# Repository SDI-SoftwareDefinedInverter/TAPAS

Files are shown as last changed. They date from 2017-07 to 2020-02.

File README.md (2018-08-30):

## SDI TAPAS - Community Inverter - Quick-Start Guide

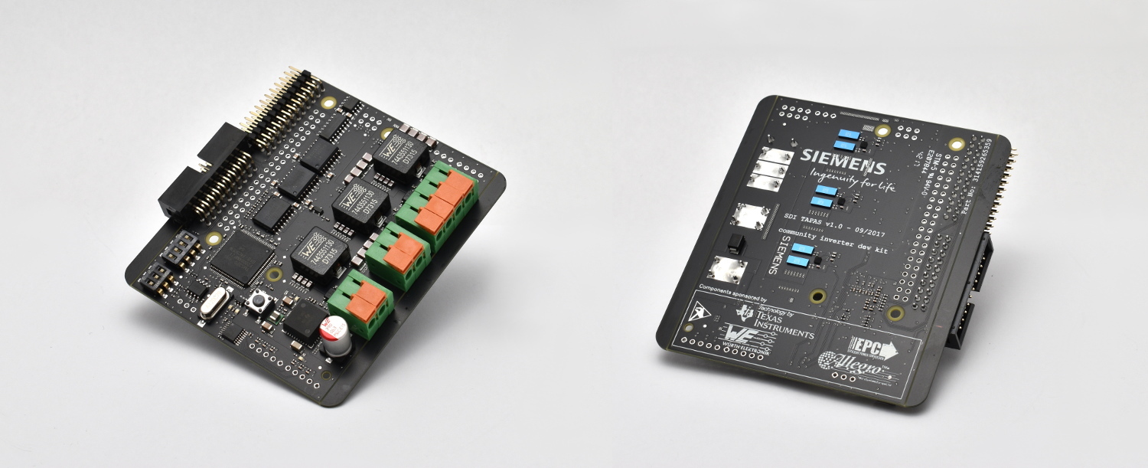
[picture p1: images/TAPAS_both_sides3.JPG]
PCB


Use your TAPAS board with Raspberry PI or Texas Instruments InstaSPIN

__!CAUTION!__

__The TAPAS community inverter board is not a toy!__ It is __intended for
laboratory use only and may only be operated by experienced personell (engineers, scientists, qualified makers). Never use it in a productive or potentially explosive environment! Never operate without supervision!__
(see section 6)

The TAPAS board as well as connected devices can get __very hot, never touch during	
operation and/or cool-down period. Always use an appropriate case.__ 

__If the TAPAS board is used in conjunction with mechanical,
electromagnetic, acoustic, optical or other components,__ e.g. a motor
drive, __significant forces can occur. Always ensure safety, containment and (mechanical) stability of the
entire set-up including case, base-plate and/or table! Prevent direct physical contact, always place set-up
in an appropriate case, employ safe software techniques__ (e.g. torque and temperature
limiting) and __limit the supply current and voltage (strictly <=48V).__

__Only enable power supply if set-up is secured in case.__

<table style="width:100%;background-color:white" cellspacing="0" cellpadding="0" border="0" >
  <tr>
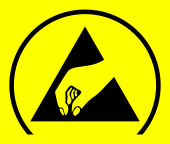
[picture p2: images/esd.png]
    <th><br>
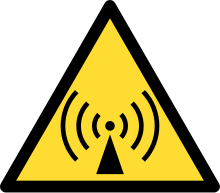
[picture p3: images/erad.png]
	 </th>
	  <th align="left"><b>
	  The TAPAS board is very sensitive to electrostatic discharge - handle with	
		  care! Never touch the board if the supply voltage is turned on!<br>
		  <br>		
The TAPAS board may emmit electromagnetic radiation! Do not operate the board in proximity to devices that are susceptible to electromagnetic interference. Do not operate if pacemaker patients are in the room.
		  </b>
	  </th>	  
  </tr>
</table>

## Foreword and acknowledgements

This board (TAPAS) is intended to train the next generation of power 
electronics researchers and (application) engineers.
It is designed as an educational platform that addresses enthusiasts as well as experts at
universities and in the industry. 

TAPAS features a 48V, 3-phase GaN power stage with on-board filters. This
design-choice allows for a high switching frequency/bandwidth (300kHz 
and beyond) whilst producing a smooth output wave-form. In contrast, 
commonly available IGBT or MOSFET converter boards typically have a 
rather limited bandwidth and/or produce a square output wave-form.

This unique feature of high bandwidth and smooth output makes TAPAS to 
some degree universal, giving rise to educational applications in AC and DC 
[drives](https://www.youtube.com/watch?v=yvK9VINiwhw&feature=youtu.be), DC/DC power conversion, [audio](https://www.youtube.com/watch?v=IIk90JD8xEQ), robotics, magnetic field control, 
battery charging, etc. Note that universality is achieved with a single, fixed 
hardware platform where the overall functionality is defined via software 
(changes) only – the reason why we coined the term “Software Defined 
Inverter” (SDI). 

TAPAS is designed of Raspberry PI and multiple boards can be used in 
collaboration, giving rise to many-phase applications such as quadrocopters 
or multi-axis servo control. Together with open-source code examples and 
extensive documentation we made TAPAS as accessible to the community as 
possible.

To help us make TAPAS affordable, we would like to thank our friends 
and partners at Texas Instruments, Efficient Power Conversion (EPC), Würth 
Elektronik and Allegro Micro who sponsored most of the active and passive 
components on the board (see bill of materials). I hope you will have as much 
fun with TAPAS as we had making it.

Dominic Buchstaller - concept, lead-design - TAPAS

*For a more visual motivation also see the [TAPAS slide deck](https://github.com/SDI-SoftwareDefinedInverter/TAPAS/blob/master/SDI_TAPAS_introduction.pdf).*

__Created by :__

SIEMENS LOGO

_SIEMENS SDI (Software Defined Inverter)_ \* in-house start-up for I/Os

__Components sponsored by:__

SPONSORS LOGO

_Texas Instruments_ <http://www.ti.com>

_Efficient power conversion (EPC)_ <http://epc-co.com>

_WÜRTH ELEKTRONIK_ <http://www.we-online.com>

_Allegro Microsystems_ <http://www.allegromicro.com>

## 1. INTRODUCTION	

This quick-start-guide will lead you through the necessary steps to get TAPAS
up and running with most commercially available DC-brushless motors.
If you are new to Texas Instruments DSPs or power conversion, we advise you	
to start with this guide. It will take you through the necessary steps to set-up 
your (coding) environment and bring the board to life. You are then free to
explore the endless possibilities that the platform provides.

### TAPAS key characteristics
+ DC-Input 12V - 48V
+ Maximum DC / AC (per phase) current - 30A
+ Up to 300W continuous power - passively cooled (@>120kHz switching frequency)
+ Switching frequency up to 600 kHz at reduced load
+ On-board output-filter enables smooth output voltage
+ Texas Instruments C2000 Piccolo (TMS320F28069M) DSP - InstaSPIN MOTION-enabled
+ CAN, GPIO, UART, SPI, 2 x QEP (encoder) interface onboard
+ Raspberry-Pi compatible

### Notice
+ Never exceed 48V operating voltage and ensure correct polarity of the power supply. Incorrect polarity will destroy the board.
+ Never short-circuit the inverter output and never enable high- and low-side switches at the same time. Always ensure the minimum dead time between switching high- and low-side switches of half-bridges. Failure to do so will most likely destroy the board.
+ In case of board failure, disconnect power source immediately. Never inhale fumes comming from the board.
+ Never disconnect the power source from the board while in operation, this may damage or destroy the board.
+ Only connect appropriate loads/sources to the board, inappropriate loads/sources (e.g. high powered generators) may damage the board
+ In order to use TAPAS with motor drives some basic information is required, in particular number of pole pairs and maximum rated current.

### TAPAS pinout
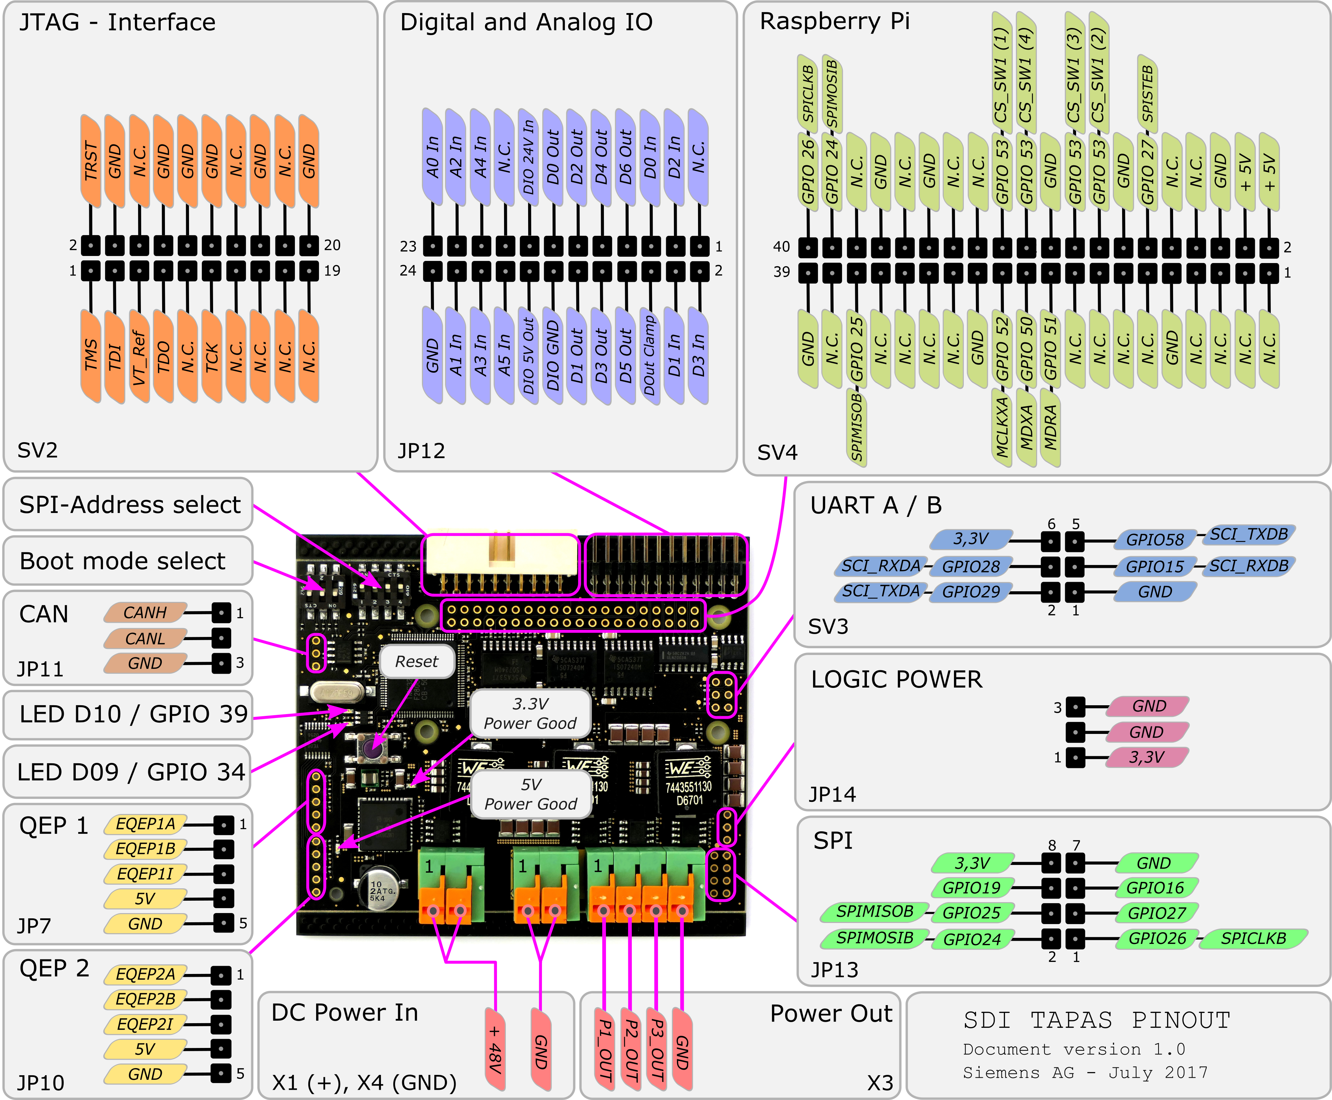
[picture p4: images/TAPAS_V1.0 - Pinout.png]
TAPAS PINOUT Figure1 : TAPAS pinout


### Box contents
+ TAPAS board
+ This quick-start guide
+ An SDI sticker
+ 7 (optional) board-connectors (JP7, JP10, JP11, JP13, JP14, SV3, SV4) for hand-soldering

### Required materials 
To get started with TAPAS you will need the following (additional) items.

+ We highly recommend placing TAPAS in __a case__. This will keep your TAPAS board safe.
The 3D model for our very own case can be found and downloaded here:
<https://github.com/SDI-SoftwareDefinedInverter/TAPAS/blob/master/TAPAShousing.zip>. 
If you don't own a 3D printer, many local 3D printing services are available on-line.
Print with temperature-stable materials like ABS (not PLA).				
+ __DC power supply__ with a minimum of 12V and >3A continuous current output.
Alternatively, you may use any battery with the correct voltage and an appropriate
fuse in the supply line	
+ A __DC brushless motor__	
+ If you want to start programming with TAPAS you will need a __JTAG programmer__.
We recommend using the OLIMEX TMS320-JTAG-USB XDS100-V2. Alternatively, you can use the newer version of this 
USB-JTAG-emulator called TMS320-XDS100v3+, there you have to leave all the jumpers open and use the __TI_JTAG_20__ 
connector to connect to your TAPAS-board with a 20pin 1:1 wired cable. 
+ If you want to use TAPAS with __Raspberry PI__ we recommend a Raspberry PI Zero (W)
+ If you want to use TAPAS with __Raspberry PI__ we also recommend the following parts for mechanical stability: 
	+ 4 screws M2,5 x 6mm (plastic)	
	+ 4 screw nuts M2,5 (plastic)
	+ 4 spacers M2,5 x 10mm with one male and one female thread (plastic)
	+ 12 washers M2,5 (plastic)

### Note: Difference between FIKAT (TAPAS pre-release version) and TAPAS (release version)
There are some PCB differences between the pre-release version (code-name FIKAT - PCB with Siemens & SDI logo) and release version 1.0 (code-name TAPAS - PCB with Siemens and manufacturer logos)

+ The connector of the OLIMEX JTAG programmer does not pysically fit into the JTAG-interface connector SV2 on FIKAT (it is too wide). You will have to solder a simple 1:1 adapter to make it work (see ugly example below). This has been fixed in TAPAS.  
+ TAPAS has more PINs of the Raspberry-Pi socket (SV4) connected to GND. On FIKAT only pins 34 and 39 are connected to GND. Hence 
you cannot use a Nano Pi with FIKAT as the GND connection is missing.
+ The SPI-Chip select signal (GPIO53) is connected to pin26 of SV4 via the address DIP-switch (2) on FIKAT. This has moved to pin 
16 of SV4 on TAPAS.
+ The resistors R\_TXA1, R\_RXA1, R\_TXB1 and R\_RXB1 are populated on FIKAT but not on TAPAS.
+ The 0Ohm gate resistors R19, R23, R20, R24, R12, R14, R16, R15, R17, R18, R22, R21 on FIKAT have been changed to 2,2Ohm on 
TAPAS
+ The DC-bus capacitor C10 for the 5V-voltage regulator U99 has been upgraded from a standard SMD-electrolytic type on FIKAT to a 
39µF polymer type on TAPAS. It can now handle a higher DC ripple current on the dc-bus
+ We added a TVS-clamping-diode for DC over voltage protection on TAPAS. (Not available on FIKAT). This is to absorb some of the 
breaking energy if the user forgot to use a breaking chopper
+ The isolation ICs IC5, IC6 and IC7 on FIKAT have been swapped for a different type on TAPAS  - this should have no influence on 
the behaviour
+ The current sensors on FIKAT are 20A bidirectional types, this has been changed to a 30A bidirectional type on TAPAS

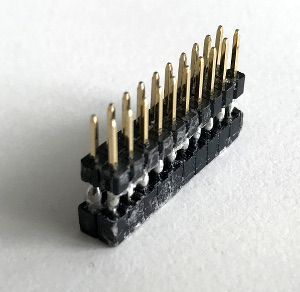
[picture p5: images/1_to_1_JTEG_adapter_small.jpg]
JTAG ADAPTER Figure1 : JTAG ADAPTER


## 2. GETTING STARTED WITH TAPAS AND RASPBERRY PI 
### (FOR LABORATORY USE ONLY)
###
### Note: TI Instaspin motor identification is not 100% reliable for every motor. Success depends on motor type, supply voltage and supply current (see below).
### Note: The stock firmware limits the board current to 6A and the board temperature to 80°C

+ Create an SD-Card image for your Raspberry Pi Zero (W)
(<https://www.raspberrypi.org/documentation/installation/installing-images/>)
+ Insert SD card in Raspberry PI Zero (W) and check that the Raspberry PI boots to a command prompt
+ Make sure that you have a working Python 3.0 and git installation

```
python --version
git --version
```
+ Get the TAPAS software and documentation package from 
<https://github.com/SDI-SoftwareDefinedInverter/TAPAS>
and place it into your home folder

```
cd
git clone https://github.com/SDI-SoftwareDefinedInverter/TAPAS.git
```
+ If successful, halt your Raspberry PI

```
sudo halt
```
+ Set the SPI-Address select DIP switch to (ON)-(OFF)-(OFF)-(OFF) for the switch 
positions from (1) - (4) (see pinout)
+ Disconnect the Raspberry PI from any power source and plug it into the TAPAS
Raspberry PI board connector (see pinout).
+ Connect your TAPAS board to a DC power supply and to a DC brushless motor (see pinout).
+ Set the supply voltage to 24V with 5A current limit and turn it on
+ If your motor does not start turning, increasing the supply voltage may help (
+ Log into your Raspberry PI and type

```
cd ~/TAPAS
python3 TAPASstart.py
```
+ Then follow the prompts on the monitor
+ If the identification fails, repeat the process and increase current/voltage limit
+ HINT: It is strongly recommended to never run the application without any motor or load connected to the terminals!

## 3. GETTING STARTED WITH TAPAS AND SIEMENS IoT2000
### (FOR LABORATORY USE ONLY)

It is rather straightforward to use TAPAS with SIMATIC IOT2000. This will allow you to build Siemens MindSphere connected drives applications and more. All you need is a few jumper-cables to connect their respective SPI interfaces.

SIMATIC IOT2040 connected to TAPAS

Required steps on SIMATIC IOT2000:
+ set-up SIMATIC IOT2000 with image V2.1.4
+ set the IO-level jumper to 3.3V (right-most jumper to right position)
+ enable SIMATIC IOT2000 SPI-interface:
```
iot2000setup
```
+ add the spidev  python library:
```
pip3 install spidev
```
+ connect the jumper cables as follows:
 
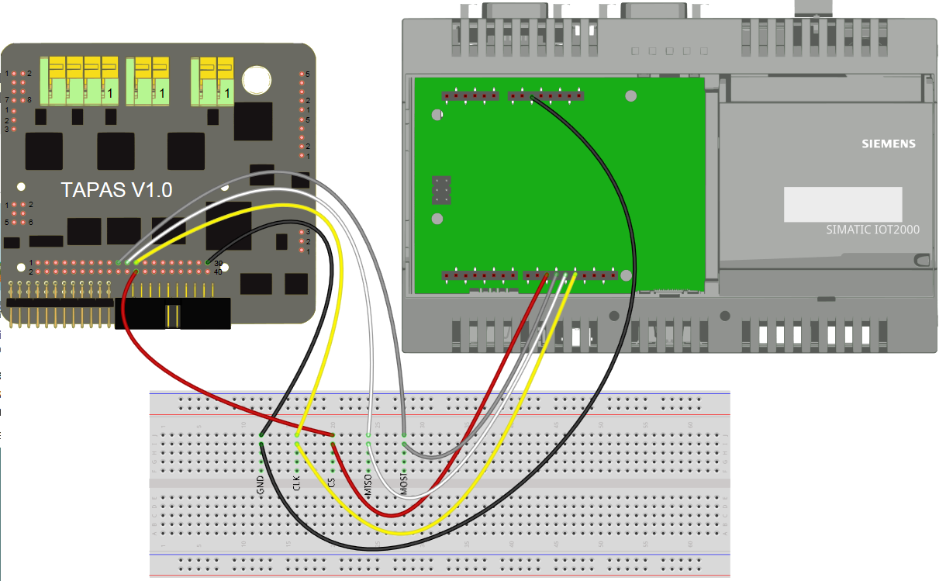
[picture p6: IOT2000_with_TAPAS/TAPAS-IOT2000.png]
SIMATIC IOT2040 - TAPAS connection instructions


+ ensure that the DIP-switch SW1 is set to ON-OFF-OFF-OFF (from position 1 to 4)
+ as git is not available on the IOT2000 platform you have to download the TAPAS-repository from github and transfer it to the IOT2000 by hand (e.g. via scp, putty, USB-Stick ... ). Then unpack it. 
+ run the TAPASstart python script: 
```
python3 TAPASstart.py
```
HINTS: 

You can find a simplified fritzing part for TAPAS here: 

<https://github.com/SDI-SoftwareDefinedInverter/TAPAS/tree/master/Fritzing_part_TAPAS>

You can find a simplified fritzing part for the SIMATIC IOT2040 and the fritzing project used to generate the cabling diagram here: 

<https://github.com/SDI-SoftwareDefinedInverter/TAPAS/tree/master/IOT2000_with_TAPAS/Fritzing>
 
Additonal images are located here: 
 
<https://github.com/SDI-SoftwareDefinedInverter/TAPAS/tree/master/IOT2000_with_TAPAS>

## 4. GETTING STARTED WITH TAPAS AND CODE COMPOSER STUDIO
### (FOR LABORATORY USE ONLY)
__!CAUTION!__	

__The stock TAPAS firmware implements software features that ensure safe operation.
Changing the stock TAPAS firmware may damage or destroy your TAPAS board, lead to
harm and/or danger. Make sure that you fully understand the supplied sample code and
the underlying principles before flashing your own firmware.__

For programming the TAPAS-Board, we recommend Code Composer Studio from Texas Instruments.
It is free of charge and can be downloaded from here:

<http://processors.wiki.ti.com/index.php/Download_CCS>

Choose the correct setup-package for your OS and install it following the instructions in
the installation-wizard.

The drivers for the OLIMEX JTAG-Debug probe are included in the standard installation
package. If you choose a JTAG Programmer from another vendor make sure that you installed
the correct drivers and that it is compatible with code composer studio.

To be able to use the InstaSpin capabilities of the DSP, you require motorware version
1\_01\_00\_16. Install git for your operating system and clone the repository in the same
way, you did it for the Raspberry Pi:

```
git clone https://github.com/SDI-SoftwareDefinedInverter/TAPAS.git
```

We included a copy of TI motorware in the cloned repository (_`motorware.zip`_). Alternatively you can download motorware from Motorware or here <https://github.com/SDI-SoftwareDefinedInverter/TAPAS/blob/master/motorware.zip>.

As the TAPAS board definition is not part of the stock motorware package we have to make some modifications to it. All the necessary changes are contained in the patch-file _`SDITAPASmotorwarePatch.patch`_. Now copy _`SDITAPASmotorwarePatch.patch`_ to the motorware installation folder (usually _`C:\ti\`_) and start git in bash mode (also in the motorware installation folder). Then execute the following commands:

```
dos2unix SDITAPASmotorwarePatch.patch
patch -p0 -i SDITAPASmotorwarePatch.patch
```

This completes the installation of motorware and you can start playing with the motorware-labs
and the quick-start demo firmware. To add the quick-start project, start Code Composer 
Studio and choose a workspace location. Close the welcome-window and then select 
"Project-\>Import CCS Projects..." In the upcoming window choose the option "Select search-directory"
and click the "Browse" - button. Navigate to the directory of your motorware installation,
go to the folder
_`<drive>:\ti\motorware\motorware_1_01_00_16\sw\solutions\instaspin_foc\boards\TAPAS_V1_0\f28x\f2806xF\projects\ccs5\`_
and click the "OK" button.

In the "Discovered projects" - list below you will see all the projects in the selected directory.
Here you can choose, for example, the _"TAPAS\_quick\_start"_ project which represents the stock demo firmware to be used with the python - script for Raspberry PI.

For all the other projects in the folders _`<drive>:\ti\motorware\motorware_1_01_00_16\sw\solutions\instaspin_foc\boards\TAPAS_V1_0\f28x\f2806xF\projects\ccs5\`_
and _`<drive>:\ti\motorware\motorware_1_01_00_16\sw\solutions\instaspin_motion\boards\TAPAS_V1_0\f28x\f2806xF\projects\ccs5\`_ please consider the _"InstaSPIN Projects and Labs User's 
Guide"_ which comes with the motorware-installation and is located 
in _`<drive>:\ti\motorware\motorware_1_01_00_16\docs\labs\instaspin_labs.pdf`_ of the motorware 
installation.There you can find further 
information on how to compile the firmware, start a debugging session, 
flash the DSP and get an impression, what all the program components 
actually do. Please keep in mind that all the labs that are designed 
to drive two motors independently are skipped - this is not possible 
with TAPAS because there is only one 3-phase power stage.

To be able to run our TAPAS demo-webapp you also require the InstaSPIN-UNIVERSALGUI from Texas Instruments which you can get here:

<http://www.ti.com/tool/INSTASPINUNIVERSALGUI>

You have now completed the installation of the TAPAS development environment. 
We have also created a TAPAS-webapp to test all external I/O hardware. 
You can download it from:	

```
https://github.com/SDI-SoftwareDefinedInverter/TAPAS/blob/master/
TAPASwebapp.zip
```
Unzip the file place it in:

```
<drive>:\ti\guicomposer\webapps\
```

## 5. FREQUENTLY ASKED QUESTIONS / TROUBLE SHOOTING

Q: Where can I get a TAPAS board?

A: The TAPAS board is provided for free – just write a few lines to tapas.support.ct@siemens.com what you intend to do with it. For legal reasons we are limited to ship the board only within the EU atm - we are working on expanding this limitation.

Q: Where can I find example projects?

A: You can find use cases and a number of user build projects on the community site <https://challenge.tapas.sdi.tools/>

Q: Can I use other JTAG-Programmers than the OLIMEX?

A: Yes you can. As long as it's 3,3V compatible and supported by Code Composer Studio it should work.

Q: Can I run the board at full power for longer periods of time?

A: Yes you can. In that case it is important to manage the board temperature. We recommend adding some temperature monitoring code (see examples)
and dynamically limit the output current. Keep the board temperature below 90°C at all times to keep your TAPAS board healthy.

Q: If I abruptly reduce the speed of my motor why is the JTAG-connection interrupted or other funny things happen?

A: It is very likely that you are using a DC power supply and not a battery to power TAPAS. The breaking energy is fed back into the DC supply and
causes an abrupt rise in DC voltage. Note that although TAPAS is designed to absorb some breaking energy, excessive DC voltage peaks may damage the
board. To prevent this effect, limit the rate of change in motor velocity, use a battery instead of a DC power supply or invest in a current sink
(breaking chopper).

Q: My motor is making some noise but does not start turning during the identification procedure from the examples. 

A: Slightly increase the supply voltage for the TAPAS-board and retry the identification of your motor. Never exceed
48V supply voltage as this will damage or even destroy your board! Also check the current rating of your motor again
and make sure you have set it correctly.

Q: I get an overcurrent protection message during motor identification in your Raspberry PI example. 

A: If this happens once, just retry the identification procedure. If this happens permanently, check your current rating again. 
Always keep in mind that the curent sensors on TAPAS can only measure +-30A at their maximum.

## 6. REFERENCES

The following documents can be helpful in developing with TAPAS:

+ TAPAS Pinout: 
<https://github.com/SDI-SoftwareDefinedInverter/TAPAS/blob/master/TAPAS-Pinout.pdf>	
+ TAPAS Schematics: 
<https://github.com/SDI-SoftwareDefinedInverter/TAPAS/blob/master/TAPAS-Schematic.pdf>
+ This 13document(quick start guide):
<https://github.com/SDI-SoftwareDefinedInverter/TAPAS/blob/master/TAPAS_quickStartGuide.pdf>
+ InstaSPIN-FOC and InstaSPIN-MOTION user guide : 
<http://www.ti.com/lit/ug/spruhj1g/spruhj1g.pdf>
+ Instaspin projects and labs user's guide, see motorware _`<drive>:\ti
\motorware\motorware_1_01_00_16\docs\labs\instaspin_labs.pdf`_
+ TMS320F28069MPZT overview and datasheet: 
<http://www.ti.com/lit/ug/spruh18g/spruh18g.pdf>

## 7. STANDARD TERMS FOR EVALUATION MODULES

1 Delivery: Siemens delivers TAPAS community converter boards (collectively, a “TAPAS BOARD or “TAPAS BOARDS”) to the User (“User”) free of charge in accordance with the terms set forth herein. User's acceptance of the TAPAS BOARD is expressly subject to the following terms.

1.1 TAPAS BOARDS ARE INTENDED SOLELY FOR PRODUCT OR SOFTWARE DEVELOPERS FOR USE IN A RESEARCH AND DEVELOPMENT SETTING TO FACILITATE FEASIBILITY EVALUATION, EXPERIMENTATION OR SCIENTIFIC ANALYSIS.  TAPAS BOARDS HAVE NO DIRECT FUNCTION AND ARE NOT FINISHED PRODUCTS. TAPAS BOARDS SHALL NOT BE DIRECTLY OR INDIRECTLY ASSEMBLED AS A PART OR SUBASSEMBLY IN ANY FINISHED PRODUCT. 

1.2 TAPAS BOARDS ARE NOT INTENDED FOR CONSUMER OR HOUSEHOLD USE. TAPAS BOARDS MAY NOT BE SOLD, SUBLICENSED, LEASED, RENTED, LOANED, ASSIGNED, OR OTHERWISE DISTRIBUTED FOR COMMERCIAL PURPOSES BY USERS, IN WHOLE OR IN PART, OR USED IN ANY FINISHED PRODUCT OR PRODUCTION SYSTEM.

2 Return and replacement:
Due to the fact that Siemens delivers the TAPAS BOARDS free of charge and for use in research and development settings only, Siemens will not provide any warranty with regard to any specifications of the TAPAS BOARDS. If the User notifies Siemens of any defects within thirty (30) days after delivery, Siemens will replace the respective TAPAS BOARD, provided that User returns the TAPAS BOARD within the 30-day-period to Siemens. Siemens will not provide any warranty for any replaced TAPAS BOARDS. 

3 Regulatory Notices:

3.1 European Union

3.1.1 For TAPAS BOARDs subject to EU Directive 2014/30/EU (Electromagnetic Compatibility Directive): This is a class A product intended for use in environments other than domestic environments that are connected to a low-voltage power-supply network that supplies buildings used for domestic purposes. In a domestic environment this product may cause radio interference in which case the user may be required to take adequate measures. 

4 TAPAS BOARD Use Restrictions and Warnings:

4.1 TAPAS BOARDS ARE NOT FOR USE IN FUNCTIONAL SAFETY AND/OR SAFETY CRITICAL EVALUATIONS, INCLUDING BUT NOT LIMITED TO EVALUATIONS OF LIFE SUPPORT APPLICATIONS.

4.2 User must read and follow the Quickstart Guide  provided by Siemens regarding the TAPAS BOARD prior to handling or using the TAPAS BOARD, including without limitation any warning or restriction notices. The notices contain important safety information related to, for example, temperatures and voltages.

4.3 Safety-Related Warnings and Restrictions:

4.3.1 User shall operate the TAPAS BOARD within Siemens’s recommended specifications and environmental considerations stated in the user guide, other available documentation provided by Siemens, and any other applicable requirements and employ reasonable and customary safeguards. Exceeding the specified performance ratings and specifications (including but not limited to input and output voltage, current, power, and environmental ranges) for the TAPAS BOARD may cause personal injury or death, or property damage. If there are questions concerning performance ratings and specifications, User should contact a Siemens TAPAS representative via the github issue tracker (https://github.com/SDI-SoftwareDefinedInverter/TAPAS/issues) prior to connecting interface electronics including input power and intended loads. Any loads applied outside of the specified output range may also result in unintended and/or inaccurate operation and/or possible permanent damage to the TAPAS BOARD and/or interface electronics. Please consult the TAPAS BOARD quick start guide prior to connecting any load to the TAPAS BOARD output. If there is uncertainty as to the load specification, please contact a Siemens field representative. During normal operation, even with the inputs and outputs kept within the specified allowable ranges, some circuit components may have elevated case temperatures. These components include but are not limited to linear regulators, switching transistors, pass transistors, current sense resistors, and heat sinks, which can be identified using the information in the associated documentation. When working with the TAPAS BOARD, please be aware that the TAPAS BOARD may become hot.

4.3.2 TAPAS BOARDs are intended solely for use by technically qualified, professional electronics experts who are familiar with the dangers and application risks associated with handling electrical mechanical components, systems, and subsystems. User assumes all responsibility and liability for proper and safe handling and use of the TAPAS BOARD by User or its employees, affiliates, contractors or designees. User assumes all responsibility and liability to ensure that any interfaces (electronic and/or mechanical) between the TAPAS BOARD and any human body are designed with suitable isolation and means to safely limit accessible leakage currents to minimize the risk of electrical shock hazard. User assumes all responsibility and liability for any improper or unsafe handling or use of the TAPAS BOARD by User or its employees, affiliates, contractors or designees.

4.4 User assumes all responsibility and liability to determine whether the TAPAS BOARD is subject to any applicable international, federal, state, or local laws and regulations related to User’s handling and use of the TAPAS BOARD and, if applicable, User assumes all responsibility and liability for compliance in all respects with such laws and regulations. User assumes all responsibility and liability for proper disposal and recycling of the TAPAS BOARD consistent with all applicable international, federal, state, and local requirements.

5 Accuracy of Information: To the extent Siemens provides information on the availability and function of TAPAS BOARDS, Siemens attempts to be as accurate as possible. However, Siemens does not warrant the accuracy of TAPAS BOARD descriptions, TAPAS BOARD availability or other information on its websites as accurate, complete, reliable, current, or error-free.

6 Disclaimers:

6.1 EXCEPT AS SET FORTH IN SECTION 2, SIEMENS DISCLAIMS ALL OTHER WARRANTIES, EXPRESS OR IMPLIED, REGARDING THE TAPAS BOARDS, INCLUDING BUT NOT LIMITED TO ANY WARRANTY OR IMPLIED WARRANTIES OF MERCHANTABILITY OR FITNESS FOR A PARTICULAR PURPOSE OR NON-INFRINGEMENT OF ANY THIRD PARTY PATENTS, COPYRIGHTS, TRADE SECRETS OR OTHER INTELLECTUAL PROPERTY RIGHTS.

6.2 EXCEPT FOR THE LIMITED RIGHT TO USE THE TAPAS BOARD SET FORTH HEREIN, NOTHING IN THESE TERMS SHALL BE CONSTRUED AS GRANTING OR CONFERRING ANY RIGHTS BY LICENSE, PATENT, OR ANY OTHER INDUSTRIAL OR INTELLECTUAL PROPERTY RIGHT OF SIEMENS, ITS SUPPLIERS/LICENSORS OR ANY OTHER THIRD PARTY, TO USE THE TAPAS BOARD IN ANY FINISHED END-USER OR READY-TO-USE FINAL PRODUCT, OR FOR ANY INVENTION, DISCOVERY OR IMPROVEMENT, REGARDLESS OF WHEN MADE, CONCEIVED OR ACQUIRED.

7 User's indemnity obligations and representations: USER WILL DEFEND, INDEMNIFY AND HOLD SIEMENS, ITS LICENSORS AND THEIR REPRESENTATIVES HARMLESS FROM AND AGAINST ANY AND ALL CLAIMS, DAMAGES, LOSSES, EXPENSES, COSTS AND LIABILITIES (COLLECTIVELY, "CLAIMS") ARISING OUT OF OR IN CONNECTION WITH ANY HANDLING OR USE OF THE TAPAS BOARD THAT IS NOT IN ACCORDANCE WITH THESE TERMS. THIS OBLIGATION SHALL APPLY WHETHER CLAIMS ARISE UNDER STATUTE, REGULATION, OR THE LAW OF TORT, CONTRACT OR ANY OTHER LEGAL THEORY, AND EVEN IF THE TAPAS BOARD FAILS TO PERFORM AS DESCRIBED OR EXPECTED.

8 Limitations on Damages and Liability:

8.1 General Limitations. IN NO EVENT SHALL SIEMENS BE LIABLE FOR ANY SPECIAL, , INDIRECT, , INCIDENTAL OR CONSEQUENTIAL, DAMAGES IN CONNECTION WITH OR ARISING OUT OF THESE TERMS OR THE USE OF THE TAPAS BOARDS. EXCLUDED DAMAGES INCLUDE, BUT ARE NOT LIMITED TO, COST OF REMOVAL OR REINSTALLATION, ANCILLARY COSTS TO THE PROCUREMENT OF SUBSTITUTE GOODS, RETESTING, OUTSIDE COMPUTER TIME, LABOR COSTS, LOSS OF GOODWILL, LOSS OF PROFITS, LOSS OF SAVINGS, LOSS OF USE, LOSS OF DATA, OR BUSINESS INTERRUPTION. NO CLAIM, SUIT OR ACTION SHALL BE BROUGHT AGAINST SIEMENS MORE THAN TWELVE (12) MONTHS AFTER THE EVENT THAT GAVE RISE TO THE CAUSE OF ACTION HAS OCCURRED.

8.2 Specific Limitations. IN NO EVENT SHALL SIEMENS’ AGGREGATE LIABILITY FROM ANY USE OF A TAPAS BOARD PROVIDED HEREUNDER, INCLUDING FROM ANY WARRANTY, INDEMITY OR OTHER OBLIGATION ARISING OUT OF OR IN CONNECTION WITH THESE TERMS EXCEED 1 EURO. THE EXISTENCE OF MORE THAN ONE CLAIM SHALL NOT ENLARGE OR EXTEND THIS LIMIT.

8.3 No limitation contained in this Section 8 or elsewhere in these Terms on the liability of Siemens shall apply to the extent that such liability is mandatory under the applicable law

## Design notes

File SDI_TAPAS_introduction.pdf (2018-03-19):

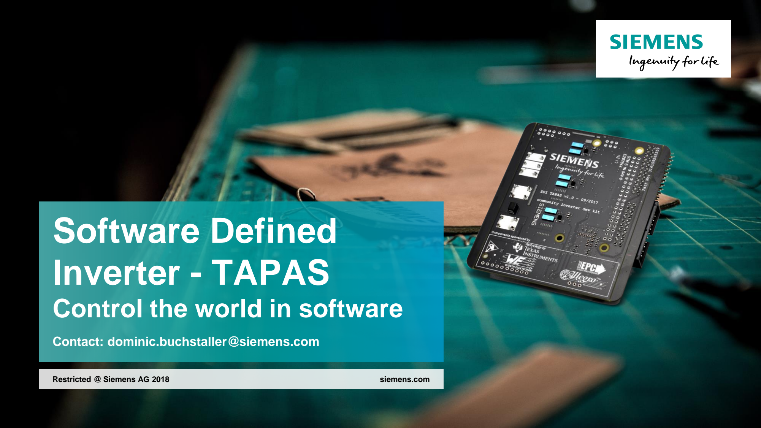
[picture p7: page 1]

# Software Defined Inverter - TAPAS

# Control the world in software

Contact: dominic.buchstaller@siemens.com

Restricted @ Siemens AG 2018 | siemens.com

Page 2 | Restricted © Siemens AG 2017 | CT REE SDI

As an algorithm developer,

# why should I care about power electronics?

As an algorithm developer,

# why should I care about power converters?

## Because I have to spend too much time on hardware!

:-) | :-) | :-)

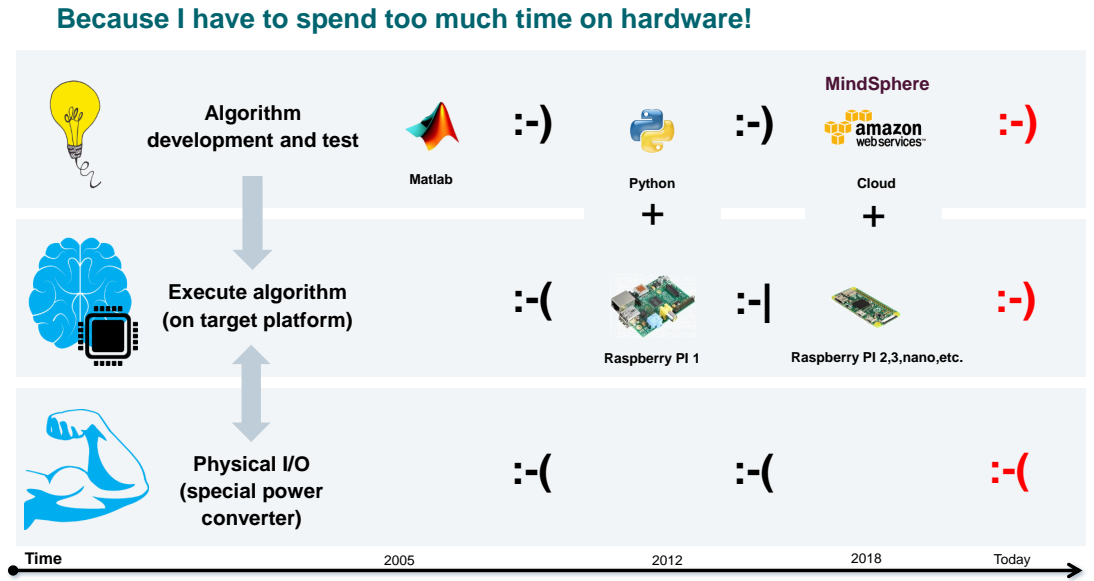
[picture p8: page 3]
Page 3; Restricted © Siemens AG 2017; CT REE SDI; Physical I/O (special power converter); Raspberry PI 1; Matlab; Time; Cloud +; Today; Python; MindSphere

Algorithm
development and test

Execute algorithm
(on target platform)

Raspberry PI 2,3,nano,etc.

## Applications for small (<50V) power converters

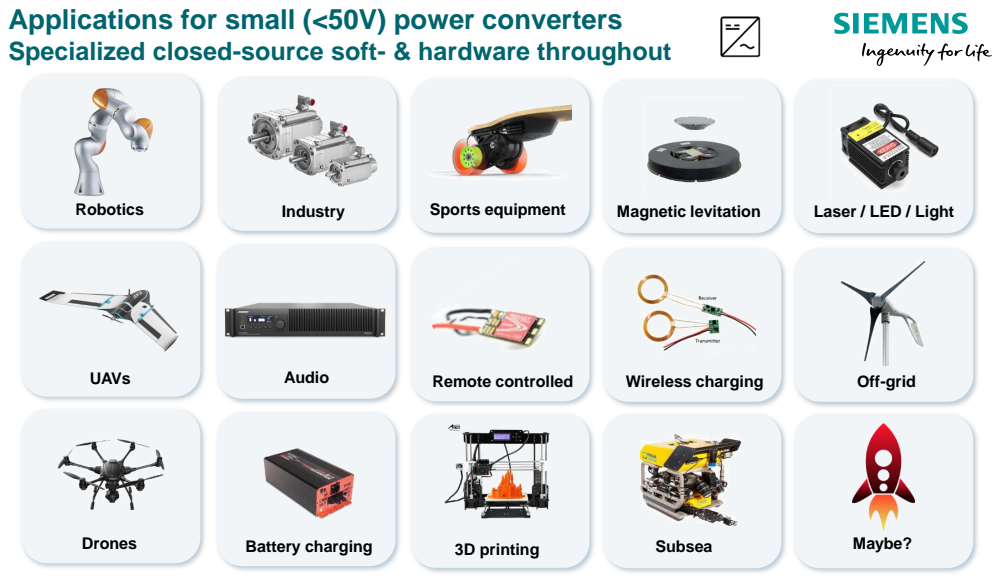
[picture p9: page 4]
Page 4; Restricted © Siemens AG 2017; CT REE SDI; Robotics; UAVs; Drones; Industry; Audio; Battery charging; Sports equipment; Remote controlled; 3D printing; Magnetic levitation; Wireless charging; Subsea; Off-grid; Maybe?

Specialized closed-source soft- & hardware throughout

Laser / LED / Light

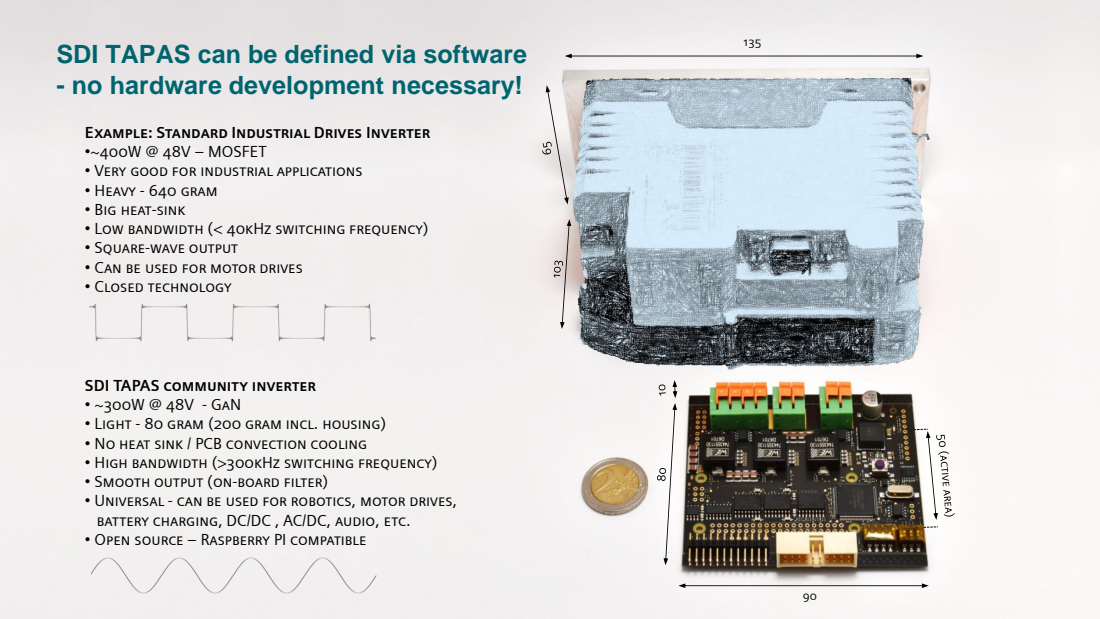
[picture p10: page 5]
Page 5; Restricted © Siemens AG 2017; CT REE SDI

SDI TAPAS can be defined via software
- no hardware development necessary!

Example: Standard Industrial Drives Inverter
•~400W @ 48V – MOSFET
• Very good for industrial applications
• Heavy - 640 gram
• Big heat-sink
• Low bandwidth (< 40kHz switching frequency)
• Square-wave output
• Can be used for motor drives
• Closed technology

SDI TAPAS community inverter
• ~300W @ 48V - GaN
• Light - 80 gram (200 gram incl. housing)
• No heat sink / PCB convection cooling
• High bandwidth (>300kHz switching frequency)
• Smooth output (on-board filter)
• Universal - can be used for robotics, motor drives,
battery charging, DC/DC , AC/DC, audio, etc.
• Open source – Raspberry PI compatible

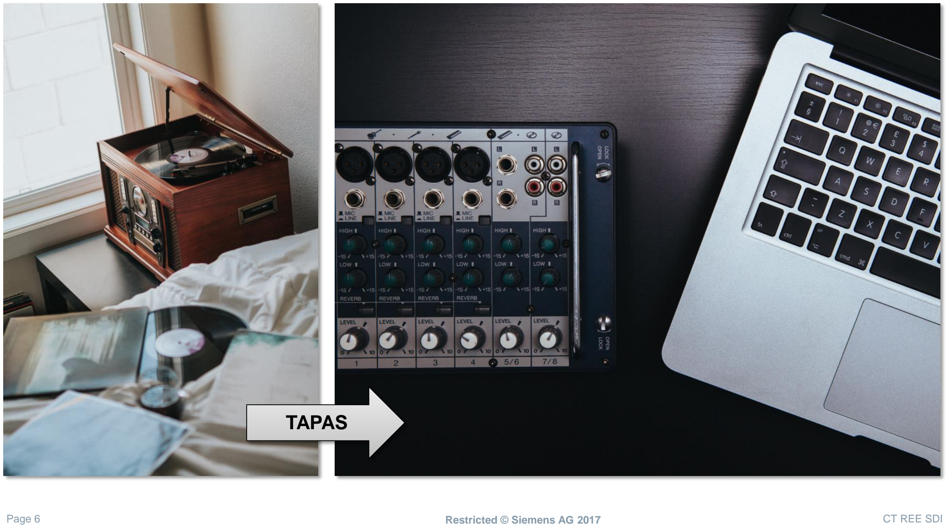
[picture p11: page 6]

Page 6 | Restricted © Siemens AG 2017 | CT REE SDI

TAPAS

## More time for algorithm development!

:-) | :-) | :-)

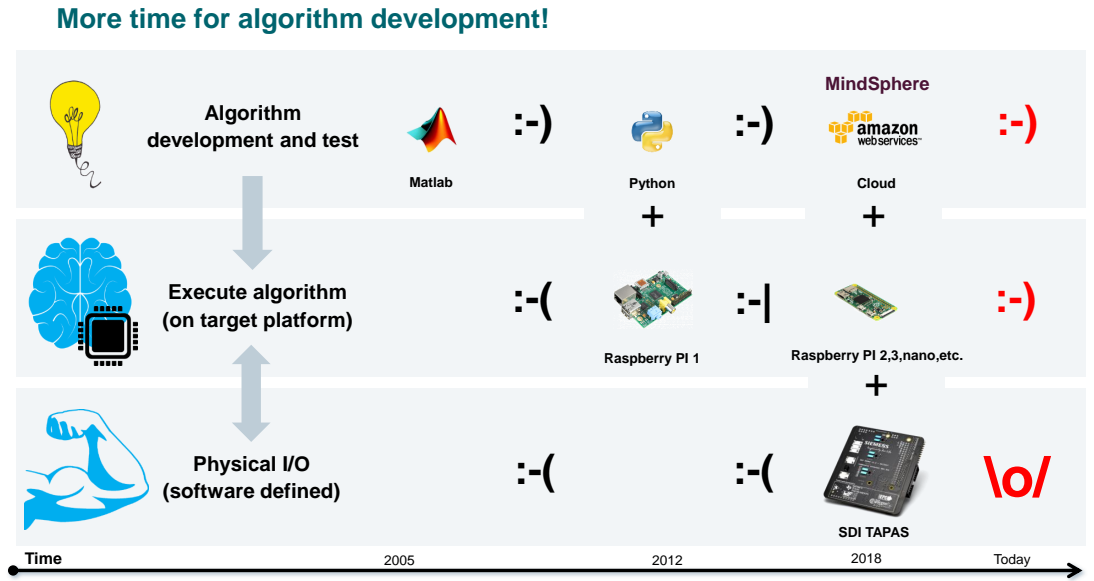
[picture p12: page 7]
Page 7; Restricted © Siemens AG 2017; CT REE SDI; Physical I/O (software defined); Raspberry PI 1; Matlab; Time; Python; Cloud; SDI TAPAS; Raspberry PI 2,3,nano,etc.; Today; MindSphere

Algorithm
development and test

Execute algorithm
(on target platform)

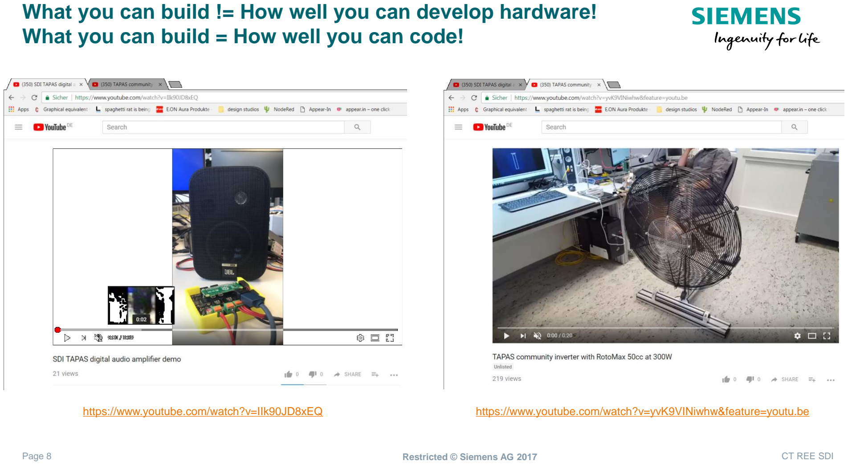
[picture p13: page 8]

Page 8 | Restricted © Siemens AG 2017 | CT REE SDI

### What you can build != How well you can develop hardware! What you can build = How well you can code!

https://www.youtube.com/watch?v=IIk90JD8xEQ | https://www.youtube.com/watch?v=yvK9VINiwhw&feature=youtu.be

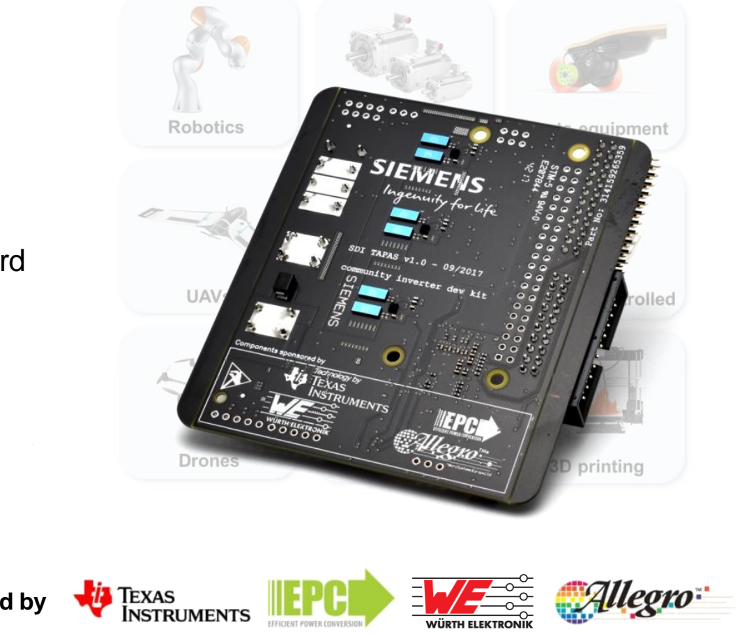
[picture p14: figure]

Page 9 | Restricted © Siemens AG 2017 | CT REE SDI

## TAPAS is not the best at everything … … but it can do lot‘s of things extremely well!

- TAPAS is available today – free of charge
- Raspberry PI compatible
- Open source software, examples & schematics

https://github.com/SDI-SoftwareDefinedInverter/

- You have a great project in mind?

Join the TAPAS community challenge and get a free board

https://challenge.tapas.sdi.tools/

- If you are a scientist, engineer or maker and would like a

board for R&D … please contact us

- Come and see us later for a demo!

*sponsored by

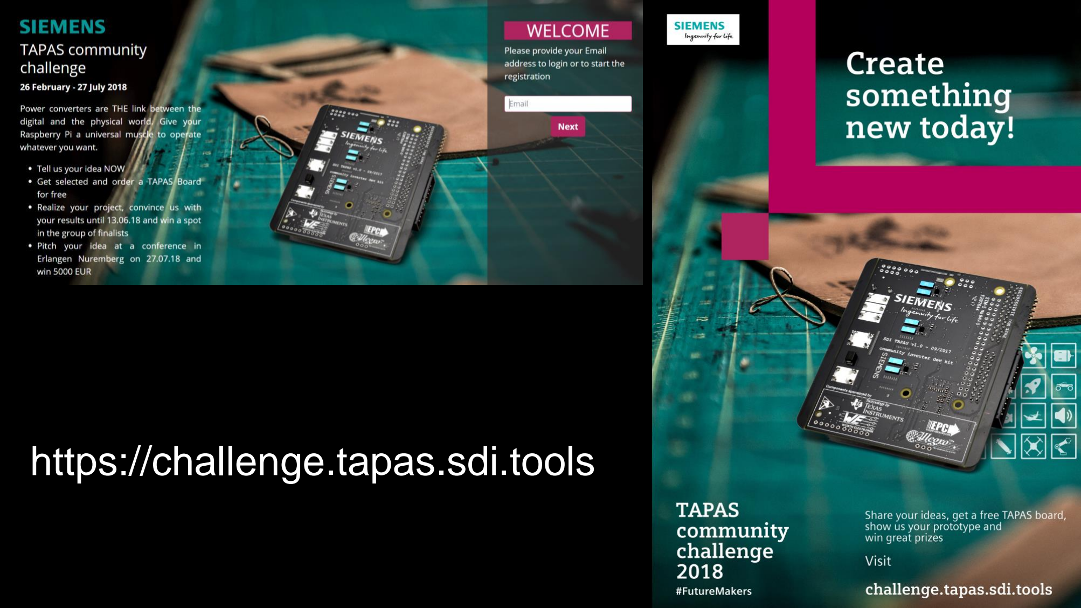
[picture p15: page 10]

Page 10 | Restricted © Siemens AG 2017 | CT REE SDI

# https://challenge.tapas.sdi.tools

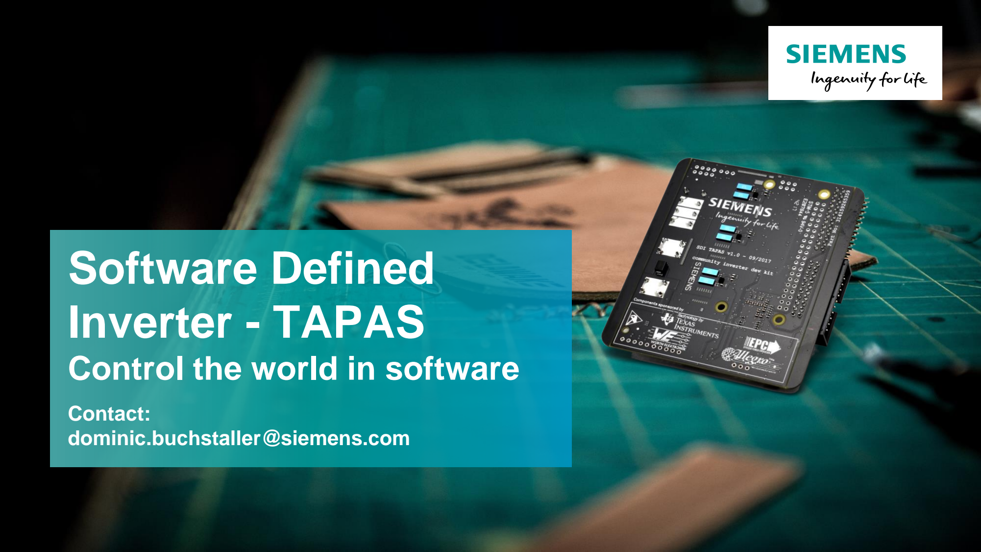
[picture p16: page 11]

# Software Defined Inverter - TAPAS

# Control the world in software

Contact:
dominic.buchstaller@siemens.com

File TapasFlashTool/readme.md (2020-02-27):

# TapasFlashTool

**it is important to remove "junk" characters from the beginning and the end of the created (hex2000.exe - I tried only on windows) text files.**

```
usage: python -m TapasFlashTool [-h] [-b B] -p port -k kernel_file -a app_file -d 
                                             {f2802x,f2803x,f2805x,f2806x,f2837xD,f2837xS,f2807x}
                                             [-b2 second_baud] [-debug]    
-h for help
```

The first baudrate is set for transferring the flash kernel, the second baudrate will be used for transferring the application file. 

## Creating the hex tables
Texas Instruments provides a tool named hex2000. It is shipped with Code Composer Studio.
Run the hex2000 programm the following:
```
hex2000 binary_file.out -boot -sci8 -a
```

Do this for your application and the flash_kernel then pass the files to the TapasFlashTool.

Tested on a Raspberry Pi with an USB to UART adapter.

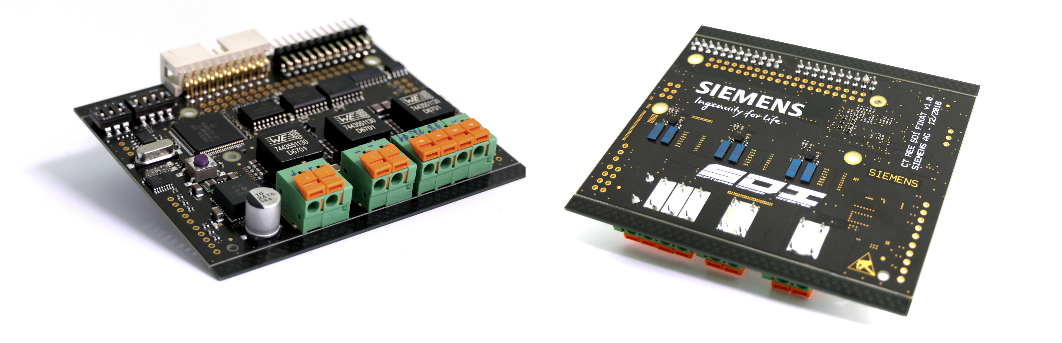
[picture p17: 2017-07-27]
images/FIKAT_all.JPG

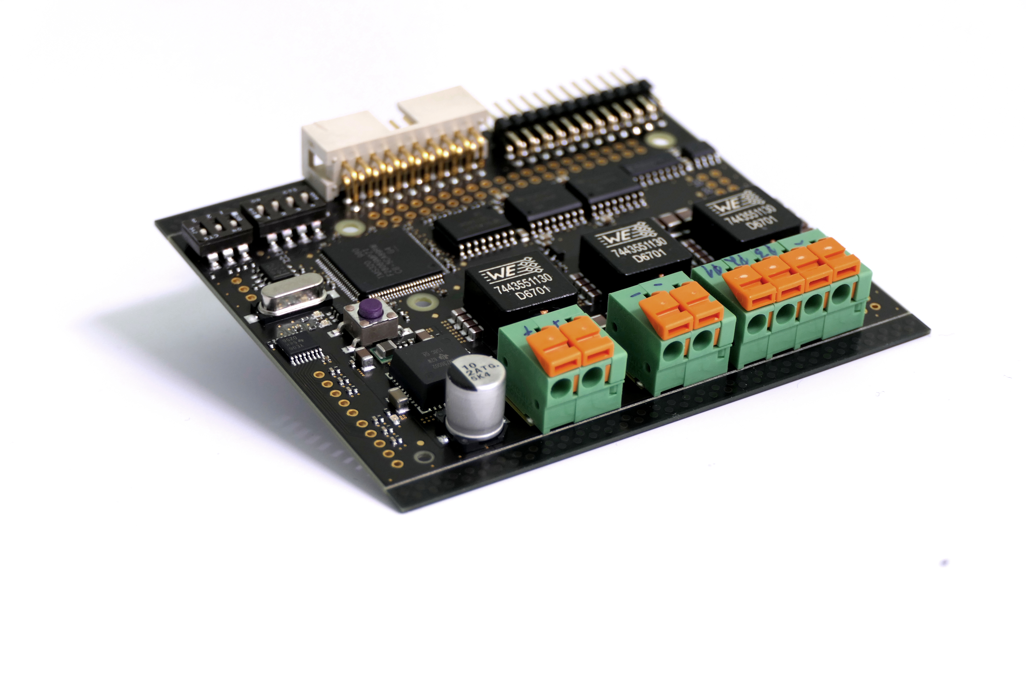
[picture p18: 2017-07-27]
images/FIKAT_top.JPG

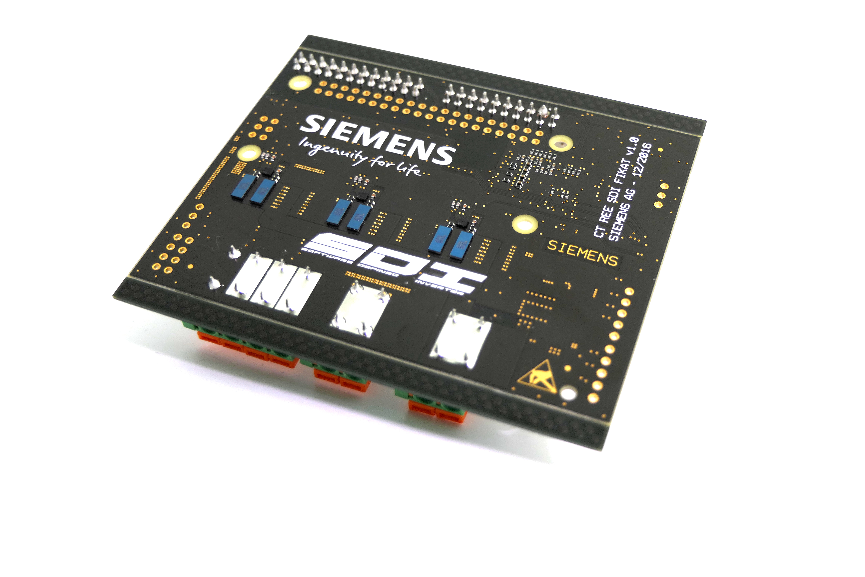
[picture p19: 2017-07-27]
images/bottom.JPG

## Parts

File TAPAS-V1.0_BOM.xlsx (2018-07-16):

Ref Des | Category | MPN | Vendor | Description | Package | Value | Tolerance | Voltage | Default | Datasheet
CS_SWITCH1 | DIP switch | 418121160804 | Wuerth | WS-DISV Flat actuator with top tape sealed | dip8gw_switch | 219-04 |  |  | populated | http://katalog.we-online.de/em/datasheet/4181211608xx.pdf
C1 | Ceramic Capacitor | 885012105007 | Wuerth | WCAP-CSGP Ceramic Capacitors, X5R Class II | 0402 | 2u2 | 20% | 6.3 | populated | http://katalog.we-online.de/pbs/datasheet/885012105007.pdf
C2 | Ceramic Capacitor | 885012105007 | Wuerth | WCAP-CSGP Ceramic Capacitors, X5R Class II | 0402 | 2u2 | 20% | 6.3 | populated | http://katalog.we-online.de/pbs/datasheet/885012105007.pdf
C3 | Ceramic Capacitor | 885012005058 | Wuerth | WCAP-CSGP Ceramic Capacitors, NP0 Class I | 0402 | 33p | 5% | 50 | populated | http://katalog.we-online.de/pbs/datasheet/885012005058.pdf
C4 | Ceramic Capacitor | 885012005058 | Wuerth | WCAP-CSGP Ceramic Capacitors, NP0 Class I | 0402 | 33p | 5% | 50 | populated | http://katalog.we-online.de/pbs/datasheet/885012005058.pdf
C5 | Ceramic Capacitor | 885012105007 | Wuerth | WCAP-CSGP Ceramic Capacitors, X5R Class II | 0402 | 2u2 | 20% | 6.3 | populated | http://katalog.we-online.de/pbs/datasheet/885012105007.pdf
C6 | Ceramic Capacitor | 885012105007 | Wuerth | WCAP-CSGP Ceramic Capacitors, X5R Class II | 0402 | 2u2 | 20% | 6.3 | populated | http://katalog.we-online.de/pbs/datasheet/885012105007.pdf
C7 | Ceramic Capacitor | 885012205018 | Wuerth | WCAP-CSGP Ceramic Capacitors, X7R Class II | 0402 | 100n | 10% | 10 | populated | http://katalog.we-online.de/pbs/datasheet/885012205018.pdf
C8 | Ceramic Capacitor | 885012205037 | Wuerth | WCAP-CSGP Ceramic Capacitors, X7R Class II | 0402 | 100n | 10% | 16 | populated | http://katalog.we-online.de/pbs/datasheet/885012205037.pdf
C9 | Ceramic Capacitor | 885012205018 | Wuerth | WCAP-CSGP Ceramic Capacitors, X7R Class II | 0402 | 100n | 10% | 10 | populated | http://katalog.we-online.de/pbs/datasheet/885012205018.pdf
C10 | Aluminum Polymer Capacitor | 875075855005 | Wuerth | WCAP-PSLC Aluminum Polymer Capacitors | k_17.26 | 39u | 20% | 63V | populated | https://katalog.we-online.de/pbs/datasheet/875075855005.pdf
C11 | Ceramic Capacitor | 885012108005 | Wuerth | WCAP-CSGP Ceramic Capacitors, X5R Class II | 1206 | 100u | -10/10% | 6V3 | populated | http://katalog.we-online.de/pbs/datasheet/885012108005.pdf
C12 | Ceramic Capacitor | 885012205064 | Wuerth | WCAP-CSGP Ceramic Capacitors, X7R Class II | 0402 | 3n3 | 10% | 50 | populated | http://katalog.we-online.de/pbs/datasheet/885012205064.pdf
C13 | Ceramic Capacitor | 885012108011 | Wuerth | WCAP-CSGP Ceramic Capacitors, X5R Class II | 1206 | 22u | 20% | 10 | populated | http://katalog.we-online.de/pbs/datasheet/885012108011.pdf
C14 | Ceramic Capacitor | 885012108011 | Wuerth | WCAP-CSGP Ceramic Capacitors, X5R Class II | 1206 | 22u | 20% | 10 | populated | http://katalog.we-online.de/pbs/datasheet/885012108011.pdf
C15 | Capacitor | C1005X7R1H104K050BB | TDK | Commercial Grade ( General (Up to 50V) ) Chip Capacitor | 0402 | 100n | 10% | 50 | populated | https://product.tdk.com/info/en/documents/chara_sheet/C1005X7R1H104K050BB.pdf
C16 | Ceramic Capacitor | 885012005061 | Wuerth | WCAP-CSGP Ceramic Capacitors, NP0 Class I | 0402 | 100p | 5% | 50 | populated | http://katalog.we-online.de/pbs/datasheet/885012005061.pdf
C17 | Ceramic Capacitor | 885012005061 | Wuerth | WCAP-CSGP Ceramic Capacitors, NP0 Class I | 0402 | 100p | 5% | 50 | populated | http://katalog.we-online.de/pbs/datasheet/885012005061.pdf
C18 | Capacitor | C2012X7S2A105K125AE | TDK | Commericial Grade ( Soft Termination ) Chip Capacitor | 0805 | 1u | 10% | 100 | populated | https://product.tdk.com/info/en/documents/chara_sheet/C2012X7S2A105K125AE.pdf
C19 | Ceramic Capacitor | 885012105007 | Wuerth | WCAP-CSGP Ceramic Capacitors, X5R Class II | 0402 | 2u2 | 20% | 6.3 | populated | http://katalog.we-online.de/pbs/datasheet/885012105007.pdf
C20 | Ceramic Capacitor | 885012105007 | Wuerth | WCAP-CSGP Ceramic Capacitors, X5R Class II | 0402 | 2u2 | 20% | 6.3 | populated | http://katalog.we-online.de/pbs/datasheet/885012105007.pdf
C21 | Ceramic Capacitor | 885012105007 | Wuerth | WCAP-CSGP Ceramic Capacitors, X5R Class II | 0402 | 2u2 | 20% | 6.3 | populated | http://katalog.we-online.de/pbs/datasheet/885012105007.pdf
C22 | Ceramic Capacitor | 885012105007 | Wuerth | WCAP-CSGP Ceramic Capacitors, X5R Class II | 0402 | 2u2 | 20% | 6.3 | populated | http://katalog.we-online.de/pbs/datasheet/885012105007.pdf
C23 | Ceramic Capacitor | 885012105007 | Wuerth | WCAP-CSGP Ceramic Capacitors, X5R Class II | 0402 | 2u2 | 20% | 6.3 | populated | http://katalog.we-online.de/pbs/datasheet/885012105007.pdf
C24 | Ceramic Capacitor | 885012205018 | Wuerth | WCAP-CSGP Ceramic Capacitors, X7R Class II | 0402 | 100n | 10% | 10 | populated | http://katalog.we-online.de/pbs/datasheet/885012205018.pdf
C25 | Capacitor | C2012X7S2A105K125AE | TDK | Commericial Grade ( Soft Termination ) Chip Capacitor | 0805 | 1u | 10% | 100 | populated | https://product.tdk.com/info/en/documents/chara_sheet/C2012X7S2A105K125AE.pdf
C26 | Ceramic Capacitor | 885012105007 | Wuerth | WCAP-CSGP Ceramic Capacitors, X5R Class II | 0402 | 2u2 | 20% | 6.3 | populated | http://katalog.we-online.de/pbs/datasheet/885012105007.pdf
C27 | Ceramic Capacitor | 885012105007 | Wuerth | WCAP-CSGP Ceramic Capacitors, X5R Class II | 0402 | 2u2 | 20% | 6.3 | populated | http://katalog.we-online.de/pbs/datasheet/885012105007.pdf
C28 | Ceramic Capacitor | 885012105007 | Wuerth | WCAP-CSGP Ceramic Capacitors, X5R Class II | 0402 | 2u2 | 20% | 6.3 | populated | http://katalog.we-online.de/pbs/datasheet/885012105007.pdf
C29 | Ceramic Capacitor | 885012105007 | Wuerth | WCAP-CSGP Ceramic Capacitors, X5R Class II | 0402 | 2u2 | 20% | 6.3 | populated | http://katalog.we-online.de/pbs/datasheet/885012105007.pdf
C30 | Ceramic Capacitor | 885012105007 | Wuerth | WCAP-CSGP Ceramic Capacitors, X5R Class II | 0402 | 2u2 | 20% | 6.3 | populated | http://katalog.we-online.de/pbs/datasheet/885012105007.pdf
C31 | Ceramic Capacitor | 885012205067 | Wuerth | WCAP-CSGP Ceramic Capacitors, X7R Class II | 0402 | 10n | 10% | 50 | populated | http://katalog.we-online.de/pbs/datasheet/885012205067.pdf
C32 | Ceramic Capacitor | 885012205067 | Wuerth | WCAP-CSGP Ceramic Capacitors, X7R Class II | 0402 | 10n | 10% | 50 | populated | http://katalog.we-online.de/pbs/datasheet/885012205067.pdf
C33 | Ceramic Capacitor | 885012205061 | Wuerth | WCAP-CSGP Ceramic Capacitors, X7R Class II | 0402 | 1n | 10% | 50 | populated | http://katalog.we-online.de/pbs/datasheet/885012205061.pdf
C34 | Ceramic Capacitor | 885012206052 | Wuerth | WCAP-CSGP Ceramic Capacitors, X7R Class II | 0603 | 1u | 10% | 16 | populated | http://katalog.we-online.de/pbs/datasheet/885012206052.pdf
C35 | Ceramic Capacitor | 885012205018 | Wuerth | WCAP-CSGP Ceramic Capacitors, X7R Class II | 0402 | 100n | 10% | 10 | populated | http://katalog.we-online.de/pbs/datasheet/885012205018.pdf
C36 | Ceramic Capacitor | 885012205061 | Wuerth | WCAP-CSGP Ceramic Capacitors, X7R Class II | 0402 | 1n | 10% | 50 | populated | http://katalog.we-online.de/pbs/datasheet/885012205061.pdf
C37 | Ceramic Capacitor | 885012205018 | Wuerth | WCAP-CSGP Ceramic Capacitors, X7R Class II | 0402 | 100n | 10% | 10 | populated | http://katalog.we-online.de/pbs/datasheet/885012205018.pdf
C38 | Ceramic Capacitor | 885012205018 | Wuerth | WCAP-CSGP Ceramic Capacitors, X7R Class II | 0402 | 100n | 10% | 10 | populated | http://katalog.we-online.de/pbs/datasheet/885012205018.pdf
C39 | Ceramic Capacitor | 885012205018 | Wuerth | WCAP-CSGP Ceramic Capacitors, X7R Class II | 0402 | 100n | 10% | 10 | populated | http://katalog.we-online.de/pbs/datasheet/885012205018.pdf
C40 | Ceramic Capacitor | 885012205037 | Wuerth | WCAP-CSGP Ceramic Capacitors, X7R Class II | 0402 | 100n | 10% | 16 | populated | http://katalog.we-online.de/pbs/datasheet/885012205037.pdf
C41 | Capacitor | C2012X7S2A105K125AE | TDK | Commericial Grade ( Soft Termination ) Chip Capacitor | 0805 | 1u | 10% | 100 | populated | https://product.tdk.com/info/en/documents/chara_sheet/C2012X7S2A105K125AE.pdf
C42 | Ceramic Capacitor | 885012205018 | Wuerth | WCAP-CSGP Ceramic Capacitors, X7R Class II | 0402 | 100n | 10% | 10 | populated | http://katalog.we-online.de/pbs/datasheet/885012205018.pdf
C43 | Capacitor | C2012X7S2A105K125AE | TDK | Commericial Grade ( Soft Termination ) Chip Capacitor | 0805 | 1u | 10% | 100 | populated | https://product.tdk.com/info/en/documents/chara_sheet/C2012X7S2A105K125AE.pdf
C44 | Ceramic Capacitor | 885012005061 | Wuerth | WCAP-CSGP Ceramic Capacitors, NP0 Class I | 0402 | 100p | 5% | 50 | populated | http://katalog.we-online.de/pbs/datasheet/885012005061.pdf
C45 | Ceramic Capacitor | 885012005061 | Wuerth | WCAP-CSGP Ceramic Capacitors, NP0 Class I | 0402 | 100p | 5% | 50 | populated | http://katalog.we-online.de/pbs/datasheet/885012005061.pdf
C46 | Ceramic Capacitor | 885012205018 | Wuerth | WCAP-CSGP Ceramic Capacitors, X7R Class II | 0402 | 100n | 10% | 10 | populated | http://katalog.we-online.de/pbs/datasheet/885012205018.pdf
C47 | Ceramic Capacitor | 885012205018 | Wuerth | WCAP-CSGP Ceramic Capacitors, X7R Class II | 0402 | 100n | 10% | 10 | populated | http://katalog.we-online.de/pbs/datasheet/885012205018.pdf
C48 | Ceramic Capacitor | 885012207098 | Wuerth | WCAP-CSGP Ceramic Capacitors, X7R Class II | 0805 | 100n | 10% | 50 | populated | http://katalog.we-online.de/pbs/datasheet/885012207098.pdf
C49 | Ceramic Capacitor | 885012207098 | Wuerth | WCAP-CSGP Ceramic Capacitors, X7R Class II | 0805 | 100n | 10% | 50 | populated | http://katalog.we-online.de/pbs/datasheet/885012207098.pdf
C50 | Ceramic Capacitor | 885012205061 | Wuerth | WCAP-CSGP Ceramic Capacitors, X7R Class II | 0402 | 1n | 10% | 50 | populated | http://katalog.we-online.de/pbs/datasheet/885012205061.pdf
C51 | Ceramic Capacitor | 885012205061 | Wuerth | WCAP-CSGP Ceramic Capacitors, X7R Class II | 0402 | 1n | 10% | 50 | populated | http://katalog.we-online.de/pbs/datasheet/885012205061.pdf
C52 | Ceramic Capacitor | 885012205061 | Wuerth | WCAP-CSGP Ceramic Capacitors, X7R Class II | 0402 | 1n | 10% | 50 | populated | http://katalog.we-online.de/pbs/datasheet/885012205061.pdf
C54 | Ceramic Capacitor | 885012205061 | Wuerth | WCAP-CSGP Ceramic Capacitors, X7R Class II | 0402 | 1n | 10% | 50 | populated | http://katalog.we-online.de/pbs/datasheet/885012205061.pdf
C55 | Ceramic Capacitor | 885012205061 | Wuerth | WCAP-CSGP Ceramic Capacitors, X7R Class II | 0402 | 1n | 10% | 50 | populated | http://katalog.we-online.de/pbs/datasheet/885012205061.pdf
C56 | Ceramic Capacitor | 885012205037 | Wuerth | WCAP-CSGP Ceramic Capacitors, X7R Class II | 0402 | 100n | 10% | 16 | populated | http://katalog.we-online.de/pbs/datasheet/885012205037.pdf
C57 | Capacitor | C1005X7R1H104K050BB | TDK | Commercial Grade ( General (Up to 50V) ) Chip Capacitor | 0402 | 100n | 10% | 50 | populated | https://product.tdk.com/info/en/documents/chara_sheet/C1005X7R1H104K050BB.pdf
C58 | Capacitor | C2012X7S2A105K125AE | TDK | Commericial Grade ( Soft Termination ) Chip Capacitor | 0805 | 1u | 10% | 100 | populated | https://product.tdk.com/info/en/documents/chara_sheet/C2012X7S2A105K125AE.pdf
C59 | Capacitor | C2012X7S2A105K125AE | TDK | Commericial Grade ( Soft Termination ) Chip Capacitor | 0805 | 1u | 10% | 100 | populated | https://product.tdk.com/info/en/documents/chara_sheet/C2012X7S2A105K125AE.pdf
C60 | Capacitor | C2012X7S2A105K125AE | TDK | Commericial Grade ( Soft Termination ) Chip Capacitor | 0805 | 1u | 10% | 100 | populated | https://product.tdk.com/info/en/documents/chara_sheet/C2012X7S2A105K125AE.pdf
C61 | Capacitor | C2012X7S2A105K125AE | TDK | Commericial Grade ( Soft Termination ) Chip Capacitor | 0805 | 1u | 10% | 100 | populated | https://product.tdk.com/info/en/documents/chara_sheet/C2012X7S2A105K125AE.pdf
C62 | Ceramic Capacitor | 885012005061 | Wuerth | WCAP-CSGP Ceramic Capacitors, NP0 Class I | 0402 | 100p | 5% | 50 | populated | http://katalog.we-online.de/pbs/datasheet/885012005061.pdf
C63 | Ceramic Capacitor | 885012005061 | Wuerth | WCAP-CSGP Ceramic Capacitors, NP0 Class I | 0402 | 100p | 5% | 50 | populated | http://katalog.we-online.de/pbs/datasheet/885012005061.pdf
C64 | Ceramic Capacitor | 885012205037 | Wuerth | WCAP-CSGP Ceramic Capacitors, X7R Class II | 0402 | 100n | 10% | 16 | populated | http://katalog.we-online.de/pbs/datasheet/885012205037.pdf
C65 | Capacitor | C1005X7R1H104K050BB | TDK | Commercial Grade ( General (Up to 50V) ) Chip Capacitor | 0402 | 100n | 10% | 50 | populated | https://product.tdk.com/info/en/documents/chara_sheet/C1005X7R1H104K050BB.pdf
C66 | Capacitor | C2012X7S2A105K125AE | TDK | Commericial Grade ( Soft Termination ) Chip Capacitor | 0805 | 1u | 10% | 100 | populated | https://product.tdk.com/info/en/documents/chara_sheet/C2012X7S2A105K125AE.pdf
C67 | Capacitor | C2012X7S2A105K125AE | TDK | Commericial Grade ( Soft Termination ) Chip Capacitor | 0805 | 1u | 10% | 100 | populated | https://product.tdk.com/info/en/documents/chara_sheet/C2012X7S2A105K125AE.pdf
C68 | Capacitor | C2012X7S2A105K125AE | TDK | Commericial Grade ( Soft Termination ) Chip Capacitor | 0805 | 1u | 10% | 100 | populated | https://product.tdk.com/info/en/documents/chara_sheet/C2012X7S2A105K125AE.pdf
C69 | Capacitor | C2012X7S2A105K125AE | TDK | Commericial Grade ( Soft Termination ) Chip Capacitor | 0805 | 1u | 10% | 100 | populated | https://product.tdk.com/info/en/documents/chara_sheet/C2012X7S2A105K125AE.pdf
C70 | Ceramic Capacitor | 885012205018 | Wuerth | WCAP-CSGP Ceramic Capacitors, X7R Class II | 0402 | 100n | 10% | 10 | populated | http://katalog.we-online.de/pbs/datasheet/885012205018.pdf
C74 | Ceramic Capacitor | 885012205018 | Wuerth | WCAP-CSGP Ceramic Capacitors, X7R Class II | 0402 | 100n | 10% | 10 | populated | http://katalog.we-online.de/pbs/datasheet/885012205018.pdf
C78 | Ceramic Capacitor | 885012205018 | Wuerth | WCAP-CSGP Ceramic Capacitors, X7R Class II | 0402 | 100n | 10% | 10 | populated | http://katalog.we-online.de/pbs/datasheet/885012205018.pdf
C81 | Ceramic Capacitor | 885012205018 | Wuerth | WCAP-CSGP Ceramic Capacitors, X7R Class II | 0402 | 100n | 10% | 10 | populated | http://katalog.we-online.de/pbs/datasheet/885012205018.pdf
C82 | Ceramic Capacitor | 885012205018 | Wuerth | WCAP-CSGP Ceramic Capacitors, X7R Class II | 0402 | 100n | 10% | 10 | populated | http://katalog.we-online.de/pbs/datasheet/885012205018.pdf
C83 | Ceramic Capacitor | 885012205018 | Wuerth | WCAP-CSGP Ceramic Capacitors, X7R Class II | 0402 | 100n | 10% | 10 | populated | http://katalog.we-online.de/pbs/datasheet/885012205018.pdf
C84 | Ceramic Capacitor | 885012205018 | Wuerth | WCAP-CSGP Ceramic Capacitors, X7R Class II | 0402 | 100n | 10% | 10 | populated | http://katalog.we-online.de/pbs/datasheet/885012205018.pdf
C85 | Ceramic Capacitor | 885012205018 | Wuerth | WCAP-CSGP Ceramic Capacitors, X7R Class II | 0402 | 100n | 10% | 10 | populated | http://katalog.we-online.de/pbs/datasheet/885012205018.pdf
C86 | Ceramic Capacitor | 885012205018 | Wuerth | WCAP-CSGP Ceramic Capacitors, X7R Class II | 0402 | 100n | 10% | 10 | populated | http://katalog.we-online.de/pbs/datasheet/885012205018.pdf
C87 | Ceramic Capacitor | 885012205018 | Wuerth | WCAP-CSGP Ceramic Capacitors, X7R Class II | 0402 | 100n | 10% | 10 | populated | http://katalog.we-online.de/pbs/datasheet/885012205018.pdf
C88 | Ceramic Capacitor | 885012205018 | Wuerth | WCAP-CSGP Ceramic Capacitors, X7R Class II | 0402 | 100n | 10% | 10 | populated | http://katalog.we-online.de/pbs/datasheet/885012205018.pdf
C89 | Ceramic Capacitor | 885012205061 | Wuerth | WCAP-CSGP Ceramic Capacitors, X7R Class II | 0402 | 1n | 10% | 50 | populated | http://katalog.we-online.de/pbs/datasheet/885012205061.pdf
C90 | Ceramic Capacitor | 885012205018 | Wuerth | WCAP-CSGP Ceramic Capacitors, X7R Class II | 0402 | 100n | 10% | 10 | populated | http://katalog.we-online.de/pbs/datasheet/885012205018.pdf
C91 | Ceramic Capacitor | 885012205018 | Wuerth | WCAP-CSGP Ceramic Capacitors, X7R Class II | 0402 | 100n | 10% | 10 | populated | http://katalog.we-online.de/pbs/datasheet/885012205018.pdf
C92 | Ceramic Capacitor | 885012207098 | Wuerth | WCAP-CSGP Ceramic Capacitors, X7R Class II | 0805 | 100n | 10% | 50 | populated | http://katalog.we-online.de/pbs/datasheet/885012207098.pdf
C93 | Ceramic Capacitor | 885012207098 | Wuerth | WCAP-CSGP Ceramic Capacitors, X7R Class II | 0805 | 100n | 10% | 50 | populated | http://katalog.we-online.de/pbs/datasheet/885012207098.pdf
C94 | Ceramic Capacitor | 885012207098 | Wuerth | WCAP-CSGP Ceramic Capacitors, X7R Class II | 0805 | 100n | 10% | 50 | populated | http://katalog.we-online.de/pbs/datasheet/885012207098.pdf
C95 | Ceramic Capacitor | 885012207098 | Wuerth | WCAP-CSGP Ceramic Capacitors, X7R Class II | 0805 | 100n | 10% | 50 | populated | http://katalog.we-online.de/pbs/datasheet/885012207098.pdf
C98 | Ceramic Capacitor | 885012205018 | Wuerth | WCAP-CSGP Ceramic Capacitors, X7R Class II | 0402 | 100n | 10% | 10 | populated | http://katalog.we-online.de/pbs/datasheet/885012205018.pdf
C100 | Ceramic Capacitor | 885012205018 | Wuerth | WCAP-CSGP Ceramic Capacitors, X7R Class II | 0402 | 100n | 10% | 10 | populated | http://katalog.we-online.de/pbs/datasheet/885012205018.pdf
C101 | Ceramic Capacitor | 885012205018 | Wuerth | WCAP-CSGP Ceramic Capacitors, X7R Class II | 0402 | 100n | 10% | 10 | populated | http://katalog.we-online.de/pbs/datasheet/885012205018.pdf
C102 | Ceramic Capacitor | 885012205018 | Wuerth | WCAP-CSGP Ceramic Capacitors, X7R Class II | 0402 | 100n | 10% | 10 | populated | http://katalog.we-online.de/pbs/datasheet/885012205018.pdf
C103 | Ceramic Capacitor | 885012207098 | Wuerth | WCAP-CSGP Ceramic Capacitors, X7R Class II | 0805 | 100n | 10% | 50 | populated | http://katalog.we-online.de/pbs/datasheet/885012207098.pdf
C104 | Ceramic Capacitor | 885012207098 | Wuerth | WCAP-CSGP Ceramic Capacitors, X7R Class II | 0805 | 100n | 10% | 50 | populated | http://katalog.we-online.de/pbs/datasheet/885012207098.pdf
C111 | Capacitor | C3225X7S2A335K200AE | TDK | Commericial Grade ( Soft Termination ) Chip Capacitor | 1210 | 3u3 | 10% | 100 | populated | https://product.tdk.com/info/en/documents/chara_sheet/C3225X7S2A335K200AE.pdf
C112 | Capacitor | C3225X7S2A335K200AE | TDK | Commericial Grade ( Soft Termination ) Chip Capacitor | 1210 | 3u3 | 10% | 100 | populated | https://product.tdk.com/info/en/documents/chara_sheet/C3225X7S2A335K200AE.pdf
C113 | Capacitor | C3225X7S2A335K200AE | TDK | Commericial Grade ( Soft Termination ) Chip Capacitor | 1210 | 3u3 | 10% | 100 | populated | https://product.tdk.com/info/en/documents/chara_sheet/C3225X7S2A335K200AE.pdf
C114 | Capacitor | C3225X7S2A335K200AE | TDK | Commericial Grade ( Soft Termination ) Chip Capacitor | 1210 | 3u3 | 10% | 100 | populated | https://product.tdk.com/info/en/documents/chara_sheet/C3225X7S2A335K200AE.pdf
C115 | Capacitor | C3225X7S2A335K200AE | TDK | Commericial Grade ( Soft Termination ) Chip Capacitor | 1210 | 3u3 | 10% | 100 | populated | https://product.tdk.com/info/en/documents/chara_sheet/C3225X7S2A335K200AE.pdf
C116 | Capacitor | C3225X7S2A335K200AE | TDK | Commericial Grade ( Soft Termination ) Chip Capacitor | 1210 | 3u3 | 10% | 100 | populated | https://product.tdk.com/info/en/documents/chara_sheet/C3225X7S2A335K200AE.pdf
C117 | Capacitor | C3225X7S2A335K200AE | TDK | Commericial Grade ( Soft Termination ) Chip Capacitor | 1210 | 3u3 | 10% | 100 | populated | https://product.tdk.com/info/en/documents/chara_sheet/C3225X7S2A335K200AE.pdf
C118 | Capacitor | C3225X7S2A335K200AE | TDK | Commericial Grade ( Soft Termination ) Chip Capacitor | 1210 | 3u3 | 10% | 100 | populated | https://product.tdk.com/info/en/documents/chara_sheet/C3225X7S2A335K200AE.pdf
C119 | Capacitor | C3225X7S2A335K200AE | TDK | Commericial Grade ( Soft Termination ) Chip Capacitor | 1210 | 3u3 | 10% | 100 | populated | https://product.tdk.com/info/en/documents/chara_sheet/C3225X7S2A335K200AE.pdf
C120 | Capacitor | C3225X7S2A335K200AE | TDK | Commericial Grade ( Soft Termination ) Chip Capacitor | 1210 | 3u3 | 10% | 100 | populated | https://product.tdk.com/info/en/documents/chara_sheet/C3225X7S2A335K200AE.pdf
C121 | Capacitor | C3225X7S2A335K200AE | TDK | Commericial Grade ( Soft Termination ) Chip Capacitor | 1210 | 3u3 | 10% | 100 | populated | https://product.tdk.com/info/en/documents/chara_sheet/C3225X7S2A335K200AE.pdf
C122 | Capacitor | C3225X7S2A335K200AE | TDK | Commericial Grade ( Soft Termination ) Chip Capacitor | 1210 | 3u3 | 10% | 100 | populated | https://product.tdk.com/info/en/documents/chara_sheet/C3225X7S2A335K200AE.pdf
D1 | LED | 150060VS75000 | Wuerth | WL-SMCW SMD Mono-color Chip LED Waterclear | 0603_led | green |  |  | populated | http://katalog.we-online.de/led/datasheet/150060VS75000.pdf
D2 | LED | 150060VS75000 | Wuerth | WL-SMCW SMD Mono-color Chip LED Waterclear | 0603_led | green |  |  | populated | http://katalog.we-online.de/led/datasheet/150060VS75000.pdf
D9 | LED | 150060VS75000 | Wuerth | WL-SMCW SMD Mono-color Chip LED Waterclear | 0603_led | green |  |  | populated | http://katalog.we-online.de/led/datasheet/150060VS75000.pdf
D10 | LED | 150060VS75000 | Wuerth | WL-SMCW SMD Mono-color Chip LED Waterclear | 0603_led | green |  |  | populated | http://katalog.we-online.de/led/datasheet/150060VS75000.pdf
D11 | Power TVS Diode | 824521481 | Wuerth | WE-TVSP Power TVS Diode | do214aa | 824521481 | 5% | 48 | populated | https://katalog.we-online.com/pbs/datasheet/824521481.pdf
IC1 | Current Sensor | ACS724LLCLU-30AB-T | Allegro MicroSystems | Automotive-Grade, Galvanically Isolated Current Sensor IC With Common-Mode Field Rejection in a Small-Footprint SOIC8 Package | SOIC 8 | ACS724LLCLU-30AB-T |  |  | populated | https://www.allegromicro.com/~/media/Files/Datasheets/ACS724-Datasheet.ashx?la=de-DE
IC2 | Current Sensor | ACS724LLCLU-30AB-T | Allegro MicroSystems | Automotive-Grade, Galvanically Isolated Current Sensor IC With Common-Mode Field Rejection in a Small-Footprint SOIC8 Package | SOIC 8 | ACS724LLCLU-30AB-T |  |  | populated | https://www.allegromicro.com/~/media/Files/Datasheets/ACS724-Datasheet.ashx?la=de-DE
IC3 | Current Sensor | ACS724LLCLU-30AB-T | Allegro MicroSystems | Automotive-Grade, Galvanically Isolated Current Sensor IC With Common-Mode Field Rejection in a Small-Footprint SOIC8 Package | SOIC 8 | ACS724LLCLU-30AB-T |  |  | populated | https://www.allegromicro.com/~/media/Files/Datasheets/ACS724-Datasheet.ashx?la=de-DE
IC4 | Darlington Transistor Array | ULN2003AD | Texas Instruments | ULN200x, ULQ200x High-Voltage, High-Current Darlington Transistor Arrays | SOIC 16 | ULN2003AD |  |  | populated | http://www.ti.com/lit/ds/symlink/uln2003a.pdf
IC5 | Digital Isolator | ISO7740DW | Texas Instruments | ISO774x High-Speed, Robust-EMC Reinforced Quad-Channel Digital Isolators | SOIC 16 | ISO7740DW |  |  | populated | http://www.ti.com/lit/ds/symlink/iso7741.pdf
IC6 | Digital Isolator | ISO7740DW | Texas Instruments | ISO774x High-Speed, Robust-EMC Reinforced Quad-Channel Digital Isolators | SOIC 16 | ISO7740DW |  |  | populated | http://www.ti.com/lit/ds/symlink/iso7741.pdf
IC7 | Digital Isolator | ISO7740DW | Texas Instruments | ISO774x High-Speed, Robust-EMC Reinforced Quad-Channel Digital Isolators | SOIC 16 | ISO7740DW |  |  | populated | http://www.ti.com/lit/ds/symlink/iso7741.pdf
IC9 | Voltage Regulator | UA78L05AIDR | Texas Instruments | UA78L00 Series Positive-Voltage Linear Regulators | SOIC 8 | UA78L05AIDR |  |  | populated | http://www.ti.com/lit/ds/symlink/ua78l.pdf
IC50 | Temperature Sensor | LM61CIM3/NOPB | Texas Instruments | LM61 2.7-V, SOT-23 or TO-92 Temperature Sensor | SOT 23 | LM61CIM3/NOPB |  |  | populated | http://www.ti.com/lit/ds/symlink/lm61.pdf
IC51 | Current Sensor | ACS724LLCLU-30AB-T | Allegro MicroSystems | Automotive-Grade, Galvanically Isolated Current Sensor IC With Common-Mode Field Rejection in a Small-Footprint SOIC8 Package | SOIC 8 | ACS724LLCLU-30AB-T |  |  | populated | https://www.allegromicro.com/~/media/Files/Datasheets/ACS724-Datasheet.ashx?la=de-DE
JP7 | Pin Header | 61300511021 | Wuerth | 2.54MM ANGLED PIN HEADER | eww0509 | 146-14-005 |  |  | not populated | http://katalog.we-online.de/em/datasheet/6130xx11021.pdf
JP10 | Pin Header | 61300511021 | Wuerth | 2.54MM ANGLED PIN HEADER | eww0509 | 146-14-005 |  |  | not populated | http://katalog.we-online.de/em/datasheet/6130xx11021.pdf
JP11 | Pin Header | 61300311021 | Wuerth | 2.54MM ANGLED PIN HEADER | eww0510 | 146-14-003 |  |  | not populated | http://katalog.we-online.de/em/datasheet/6130xx11021.pdf
JP12 | Pin Header | 61302421021 | Wuerth | 2.54MM ANGLED DUAL PIN HEADER | eww0511 | 147-14-024 |  |  | populated | http://katalog.we-online.de/em/datasheet/6130xx21021.pdf
JP13 | Pin Header | 61300821021 | Wuerth | 2.54MM ANGLED DUAL PIN HEADER | eww0512 | 147-14-008 |  |  | not populated | http://katalog.we-online.de/em/datasheet/6130xx21021.pdf
JP14 | Pin Header | 61300311021 | Wuerth | 2.54MM ANGLED PIN HEADER | eww0510 | 146-14-003 |  |  | not populated | http://katalog.we-online.de/em/datasheet/6130xx11021.pdf
L4 | Ferrite Bead | BLM15PD600SN1D | Murata | Chip Ferrite Bead | 0402 | BLM15PD600SN1D | - |  | populated | https://www.murata.com/en-us/products/productdata/8796740059166/ENFA0018.pdf
L5 | Chip Bead Inductor | BKP1005HS221-T | Taiyo Yuden | Multilayer Chip Bead Inductors for Power Lines (BK series P type) | 0402 | BKP1005HS221-T | - |  | populated | http://ds.yuden.co.jp/TYCOMPAS/ut/detail.do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
L6 | Inductor | 7443551130 | Wuerth | WE-HCI SMD Flat Wire High Current Inductor | eww0504 | 1.3uH/25A | 20% |  | populated | http://katalog.we-online.de/pbs/datasheet/7443551130.pdf
L7 | Inductor | 7443551130 | Wuerth | WE-HCI SMD Flat Wire High Current Inductor | eww0504 | 1.3uH/25A | 20% |  | populated | http://katalog.we-online.de/pbs/datasheet/7443551130.pdf
L8 | Inductor | 7443551130 | Wuerth | WE-HCI SMD Flat Wire High Current Inductor | eww0504 | 1.3uH/25A | 20% |  | populated | http://katalog.we-online.de/pbs/datasheet/7443551130.pdf
Q1 | Crystal | ABLS-12.000MHZ-B2-T | ABRACON CORPORATION | HC/49US (AT49) SMD LOW PROFILE CRYSTAL ABLS | HC-49/U-S | 12MHz |  |  | populated | https://abracon.com/Resonators/abls.pdf
RBFT1 | Chip Resistor | 737-9120 | RS-Pro | RS Pro RS Series Thick Film Surface Mount Fixed Resistor 0402 Case 10kΩ ±1% 0.063W ±100ppm/°C | 0402 | 10K | 1% |  | populated | https://docs-emea.rs-online.com/webdocs/157b/0900766b8157b5ae.pdf
RFBB1 | Chip Resistor | ERJ2RKF1203X | Panasonic | Precision Thick Film Chip Resistors | 0402 | 120K | 1% |  | populated | https://industrial.panasonic.com/cdbs/www-data/pdf/RDA0000/AOA0000C304.pdf
RPG1 | Chip Resistor | RC0402FR-0739KL | YAGEO | GENERAL PURPOSE CHIP RESISTORS | 0402 | 39K | 1% |  | populated | http://www.yageo.com/documents/recent/PYu-RC_Group_51_RoHS_L_9.pdf
R_MISO_0 | Chip Resistor | RC0402JR-070RL | YAGEO | GENERAL PURPOSE CHIP RESISTORS | 0402 | 0R | 1% |  | populated | http://www.yageo.com/documents/recent/PYu-RC_Group_51_RoHS_L_9.pdf
R_MISO_1 | Chip Resistor | RC0402JR-070RL | YAGEO | GENERAL PURPOSE CHIP RESISTORS | 0402 | 0R | 1% |  | populated | http://www.yageo.com/documents/recent/PYu-RC_Group_51_RoHS_L_9.pdf
R_MOSI_0 | Chip Resistor | RC0402JR-070RL | YAGEO | GENERAL PURPOSE CHIP RESISTORS | 0402 | 0R | 1% |  | populated | http://www.yageo.com/documents/recent/PYu-RC_Group_51_RoHS_L_9.pdf
R_MOSI_1 | Chip Resistor | RC0402JR-070RL | YAGEO | GENERAL PURPOSE CHIP RESISTORS | 0402 | 0R | 1% |  | populated | http://www.yageo.com/documents/recent/PYu-RC_Group_51_RoHS_L_9.pdf
R_RXA1 | Chip Resistor | RC0402JR-070RL | YAGEO | GENERAL PURPOSE CHIP RESISTORS | 0402 | 0R | 1% |  | not populated | http://www.yageo.com/documents/recent/PYu-RC_Group_51_RoHS_L_9.pdf
R_RXB1 | Chip Resistor | RC0402JR-070RL | YAGEO | GENERAL PURPOSE CHIP RESISTORS | 0402 | 0R | 1% |  | not populated | http://www.yageo.com/documents/recent/PYu-RC_Group_51_RoHS_L_9.pdf
R_SCLK_0 | Chip Resistor | RC0402JR-070RL | YAGEO | GENERAL PURPOSE CHIP RESISTORS | 0402 | 0R | 1% |  | populated | http://www.yageo.com/documents/recent/PYu-RC_Group_51_RoHS_L_9.pdf
R_SCLK_1 | Chip Resistor | RC0402JR-070RL | YAGEO | GENERAL PURPOSE CHIP RESISTORS | 0402 | 0R | 1% |  | populated | http://www.yageo.com/documents/recent/PYu-RC_Group_51_RoHS_L_9.pdf
R_SPI_0_CS | Chip Resistor | RC0402JR-070RL | YAGEO | GENERAL PURPOSE CHIP RESISTORS | 0402 | 0R | 1% |  | populated | http://www.yageo.com/documents/recent/PYu-RC_Group_51_RoHS_L_9.pdf
R_SPI_1_CS | Chip Resistor | RC0402JR-070RL | YAGEO | GENERAL PURPOSE CHIP RESISTORS | 0402 | 0R | 1% |  | populated | http://www.yageo.com/documents/recent/PYu-RC_Group_51_RoHS_L_9.pdf
R_TXA1 | Chip Resistor | RC0402JR-070RL | YAGEO | GENERAL PURPOSE CHIP RESISTORS | 0402 | 0R | 1% |  | not populated | http://www.yageo.com/documents/recent/PYu-RC_Group_51_RoHS_L_9.pdf
R_TXB1 | Chip Resistor | RC0402JR-070RL | YAGEO | GENERAL PURPOSE CHIP RESISTORS | 0402 | 0R | 1% |  | not populated | http://www.yageo.com/documents/recent/PYu-RC_Group_51_RoHS_L_9.pdf
R1 | Chip Resistor | 804-7158 | RS-Pro | RS Pro Thick Film Surface Mount Resistor 0402 Case 1kΩ ±1% 0.0625W ±100ppm/°C | 0402 | 1K | 1% |  | populated | https://docs-emea.rs-online.com/webdocs/157c/0900766b8157cabc.pdf
R2 | Chip Resistor | 804-7127 | RS-Pro | RS Pro Thick Film Surface Mount Resistor 0402 Case 510Ω ±1% 0.0625W ±100ppm/°C | 0402 | 510R | 1% |  | populated | https://docs-emea.rs-online.com/webdocs/157c/0900766b8157cab3.pdf
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

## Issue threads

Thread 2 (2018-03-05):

How to get one TAPAS board?

zvonko-gmail-com, 2018-03-05:
Please instruct me how to applay for a TAPAS board.
Thanks,
zvonko@gmail.com

SDI-SoftwareDefinedInverter, 2018-03-06:
Join the TAPAS community challenge https://challenge.tapas.sdi.tools/, pitch an idea and get a free board. There are also neat prizes to win - if you like that kind of thing.

Closed 2018-03-06.

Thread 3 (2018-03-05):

How to obtain a TAPAS board?

waldhol, 2018-03-05:
I'd like to get one.
Where can I get it and how much does it cost?
holger.waldmann@web.de

SDI-SoftwareDefinedInverter, 2018-03-06:
Join the TAPAS community challenge https://challenge.tapas.sdi.tools/, pitch an idea and get a free board! There are also neat prizes to win - if you like that kind of thing.

Closed 2018-03-06.

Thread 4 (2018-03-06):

Getting a TAPAS

bjjohns, 2018-03-06:
I too would like to get a tapas board. Please let me know how.

SDI-SoftwareDefinedInverter, 2018-03-06:
Join the TAPAS community challenge <https://challenge.tapas.sdi.tools/>, pitch an idea and get a free board. There are also neat prizes to win - if you like that kind of thing.

Closed 2018-03-06.

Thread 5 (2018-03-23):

bill of materials

minority24, 2018-03-23:
Would you be able to upload a bill of materials as well?

SDI-SoftwareDefinedInverter, 2018-09-03:
Hi minority24,

a bill of materials was checked and uploaded.

You can find it here:
https://github.com/SDI-SoftwareDefinedInverter/TAPAS/blob/master/TAPAS-V1.0_BOM.xlsx

Thanks for the hint, the bill of materials for the new, coming version of TAPAS will come directly when the new board is available.

Closed 2018-09-03.

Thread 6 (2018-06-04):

Connection to Debug Probe not Possible

RealAndy1, 2018-06-04:
I tried to connect the TAPAS Board via XDSv3 Debugger (Included on the SmartRF06 Board) to the PC to control it via the WebApp. It was not working until I Removed R8 and R9. The Datasheet on page 11 cleary state that
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

Flydroid, 2018-07-28:
Running Code Composer Studio 8.1 and the XDS110  debug probe, i also couldn't connect to the board.
I removed the resistors the otherway around first R8 and then R9, however the emulator error stays (was not able to circulate the bits).

I'm powering the board over 3.3V from the debug probe. Nothing connected on the DC power In.

SDI-SoftwareDefinedInverter, 2018-09-03:
Can you tell me, why you do power the board from the debug probe?
Does the debug probe supply sufficient current on the 3,3V line?

RealAndy1, 2018-09-03:
The probe does supply enough current to program the µC. But you can also power the µC externally. If you do so, please set the jumper of the debugger in a position that it does not power the µC. Otherwise you may kill the debugger.

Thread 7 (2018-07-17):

ADC_buffers

r0n4n, 2018-07-17:
Hello,

I have a questions about the values returned by the ADC. Are they signed or not ?
Because, for instance, the output voltages are alternating, and there are just some voltage divisers before the ADC but no offset. And if I'm not wrong, the input range of the ADC are from 0 to 3.3V.
So how do you get the negative value of the output voltage ?

Thank you for your help,

Ronan

SDI-SoftwareDefinedInverter, 2018-09-03:
Hello,

first to answer your question:
The values of the ADC are of course not signed.  But there is also no reason, why this should be necessary. Every phase voltage and also the dc-bus voltage is measured against GND of the TAPAS
and therefore it's values are always positive. You are right, that the input range of the ADC is from 0 - 3,3V.
There must never be a negative output voltage of the TAPAS seen against GND, as this will destroy the board.

Best
Andreas @ TAPAS Team

Closed 2018-09-03.

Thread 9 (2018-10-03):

Patch can't find file to patch at input line 4

lambda-gnd, 2018-10-03:
Hello,
after trying to apply the patch at ~/ti
with the command patch `-p0 -i SDITAPASmotorwarePatch.patch
`
 i get the message

```
can't find file to patch at input line 4
Perhaps you used the wrong -p or --strip option?
The text leading up to this was:
--------------------------
|diff -u -r --new-file motorware/motorware_1_01_00_16/sw/drivers/clk/src/32b/f28x/f2806x/clk.c motorware_modified/motorware_1_01_00_16/sw/drivers/clk/src/32b/f28x/f2806x/clk.c
|--- motorware/motorware_1_01_00_16/sw/drivers/clk/src/32b/f28x/f2806x/clk.c	2015-01-20 16:29:02.000000000 +0100
|+++ motorware_modified/motorware_1_01_00_16/sw/drivers/clk/src/32b/f28x/f2806x/clk.c	2017-11-29 13:39:29.416771900 +0100
--------------------------
File to patch:

```

TrangSiegen, 2019-01-25:
I had the same problems. Anyone has some solutions for me?

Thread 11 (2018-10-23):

Raspberry Pi Program doesn't do identification

phdaf, 2018-10-23:
the raspberry pi python program (TAPASstart) doesn't seem to enter the while-loop in the identification mode.
"while ((ret["flags"] & (1 << 5)) == 0):" never gets true.
what does this flag show? or has anyone got a similar problem?
thanks in advance!

Splash005, 2018-11-07:
Hello Phdaf,

it worked for me. The flag shows that the motor is identified. If Bit5 is still =0 the identification data are send to the TAPAS. If it turns true, the identification is done and the motor-parameters can be saved.

Do you have a generel SPI connection to the board? What does it show when you press 2 for identification? Did it succeed?

phdaf, 2018-11-07:
hey splash,

thanks for your answer!
i think there is actually no spi connection to the TAPAS! do you know where i can find a test program for ccs to test the spi of the TAPAS (by connecting MOSI and MISO)?

Splash005, 2018-11-07:
Hello,
You probably would need a Jtag adapter for connecting to the TAPAS board with CCS. I would try to do the search on the raspberry side.

1.  How have you connected the raspberry to the tapas board? Did you put it on the Raspberry connection or did you use the SPI-Connectors?
2.  Have you selected the DIP-Switches on the TAPAS-Board to ON-OFF-OFF-OFF (testwise you can also put all on ON)
3.  Have you double-checked the correct Pin-assignment? tapas-Miso to rasp-Mosi and so on

I connected for example just the manditory PINS and for that I used the MCLKXA, MDXA, MDRA, CS_SW_1, 5V and GND pins from the Tapas board to the raspberry.

Good Luck! :)

phdaf, 2018-11-08:
hey splash,

thanks again!
i have got a jtag programmer and i already tested the raspi spi with a test program (and it worked fine).

i put on the raspi connection to connect to the tapas and i tried all DIP-switches combinations. i guess the pins must be correct when i put the raspberry directly on the board (and according to the pinouts the assignment is right)

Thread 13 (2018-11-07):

TAPAS_quick_start (Code Composer Studio)

Splash005, 2018-11-07:
Dear Tapas-Team,

You define in the TAPAS_Quick_start program (which is probably precompiled on the TAPAS board?) some global Variables.
To be precise I mean the TAPAS_UPPER_TEMP_LIMIT (Line 69) and TAPAS_UPPER_CURRENT_LIMIT (line 71).
So is it generally correct that with the standard programm I can not drive a motor with a higher current then 6 Amps (the definition of upper_current_limit) ?

Also I think you might have a programm error in the code:
In the Main-loop where you Loop while the enableSys Flag = false
you check the temperature and current again (Line 293 and 301).

When the enableSys_Flag = true you enter the next While loop and there you check the temp and current again (Line 392 and398). But now you check for 60 Degrees and 2 Amps instead of the defined global variables. I assume that it is supposed to be the global Variables upper_temp_limit and upper_current_limit

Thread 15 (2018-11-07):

USER_ADC_FULL_SCALE_CURRENT_A ??????????????

karu2003, 2018-11-07:
Hello,

How did you find this #define USER_ADC_FULL_SCALE_CURRENT_A (69.7)?

3.3 / 69.7 = 0.04734V/А. ??????????????????

You have a divider 10/22 = 0.4545

You have ACS724LLCTR-30AB-T - 0.066V/A    0.066V/A * 0.4545 = 0.02997V/A

30А * 0.066V/А = 1.98V    1.98V * 0.4545 = 0.899V

Imax = 2.5V / 0.066V/A = 37.879A Ifull = 75.758A

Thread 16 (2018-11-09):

Motor identification error

bondCH, 2018-11-09:
Dear Community
We are trying to get the TAPAS board up and running with a Raspberry Pi. We have tried with a 750W and a 150W BLDC.
When identifying the BLDC at the end of flux measurement, the engine brakes abruptly to zero speed. (see p.249, User's guide InstaSPIN-FOC & InstaSPIN-Motion)
The program changes to the idel state without first making the Ls measurement and all values   already measured are reset to zero. The identification of the engine can therefore not be completed or it sets an `overcurrent error`.
Before `Rated_Flux` State the program is in` Rated_Flux_ol`. Therefore, we exclude that an 'ACIM machine' is set as default and a `lock_rotor` is set.

the following attempts have already been made:

-Parallel switching of power resistors when feeding the TAPAS to intercept feedback (Overcurrent_Error)
- DC power supply between 10 and 30V.
- Different motor maximum currents between 10 and 50A (750W BLDC) / 5 and 15A (150W BLDC).
- Different fluxEstFrequency between 10 and 100Hz in 10Hz steps (see p.300, user's guide InstaSPIN-  FOC & InstaSPIN-Motion)

Thanks for any feedback
With kind regards
I.Bond

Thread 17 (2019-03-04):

Filter design - inductances too small

workoft, 2019-03-04:
When experimenting with the FIKAT board, I noticed that the inductances are tiny. For a DC-link voltage of 48V, 50% duty cycle and 24V output voltage at 150kHz, the current ripple is 61.5A. In reality, the duty cycle won't always be 50% and the output voltage at the filter capacitors isn't constant, so the average current ripple will be less on average, but just a bit, not by orders of magnitude.

This causes the semiconductors to heat up even at small loads. Running an induction machine at about 0.5A peak heated the chips to about 100 °C (thermal camera). Removing the filter capacitors alleviated the problem for this setup. The machine's inductance is quite large, so the current was sufficiently filtered, unfortunately the steep voltage slopes on the wire to the machine caused the connection to the debugger to break as soon as PWM was turned on. But the chips barely exceeded 40°C

For small loads, the 1.3uH inductors can be replaced by 33uH inductors in the same package. This reduces the current ripple to 2.4A, which is still fairly large, but acceptable. Unfortunately these inductors have a rated current of 5.5A, which is too small for larger loads. Alternatively, inductors can be added externally (given that the capacitors are removed), but that will cause the voltage at the sensors to jump as this creates an inductive voltage divider between the output voltage and the switched voltage.

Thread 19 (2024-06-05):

Why 48V and 24V DC Input

DarthiDu, 2024-06-05:
Hi,
why does the inverter have two DC Inputs. One for 48V Power in at X1 and one at JP 12 Pin15 with 24V DIO24IN. The 24 DIO24IN, seems to be just for the Digital Components, but why both are splitted? And how you would solve the power supply for the 24V extra?
Thank you!

Closed 2024-08-10.

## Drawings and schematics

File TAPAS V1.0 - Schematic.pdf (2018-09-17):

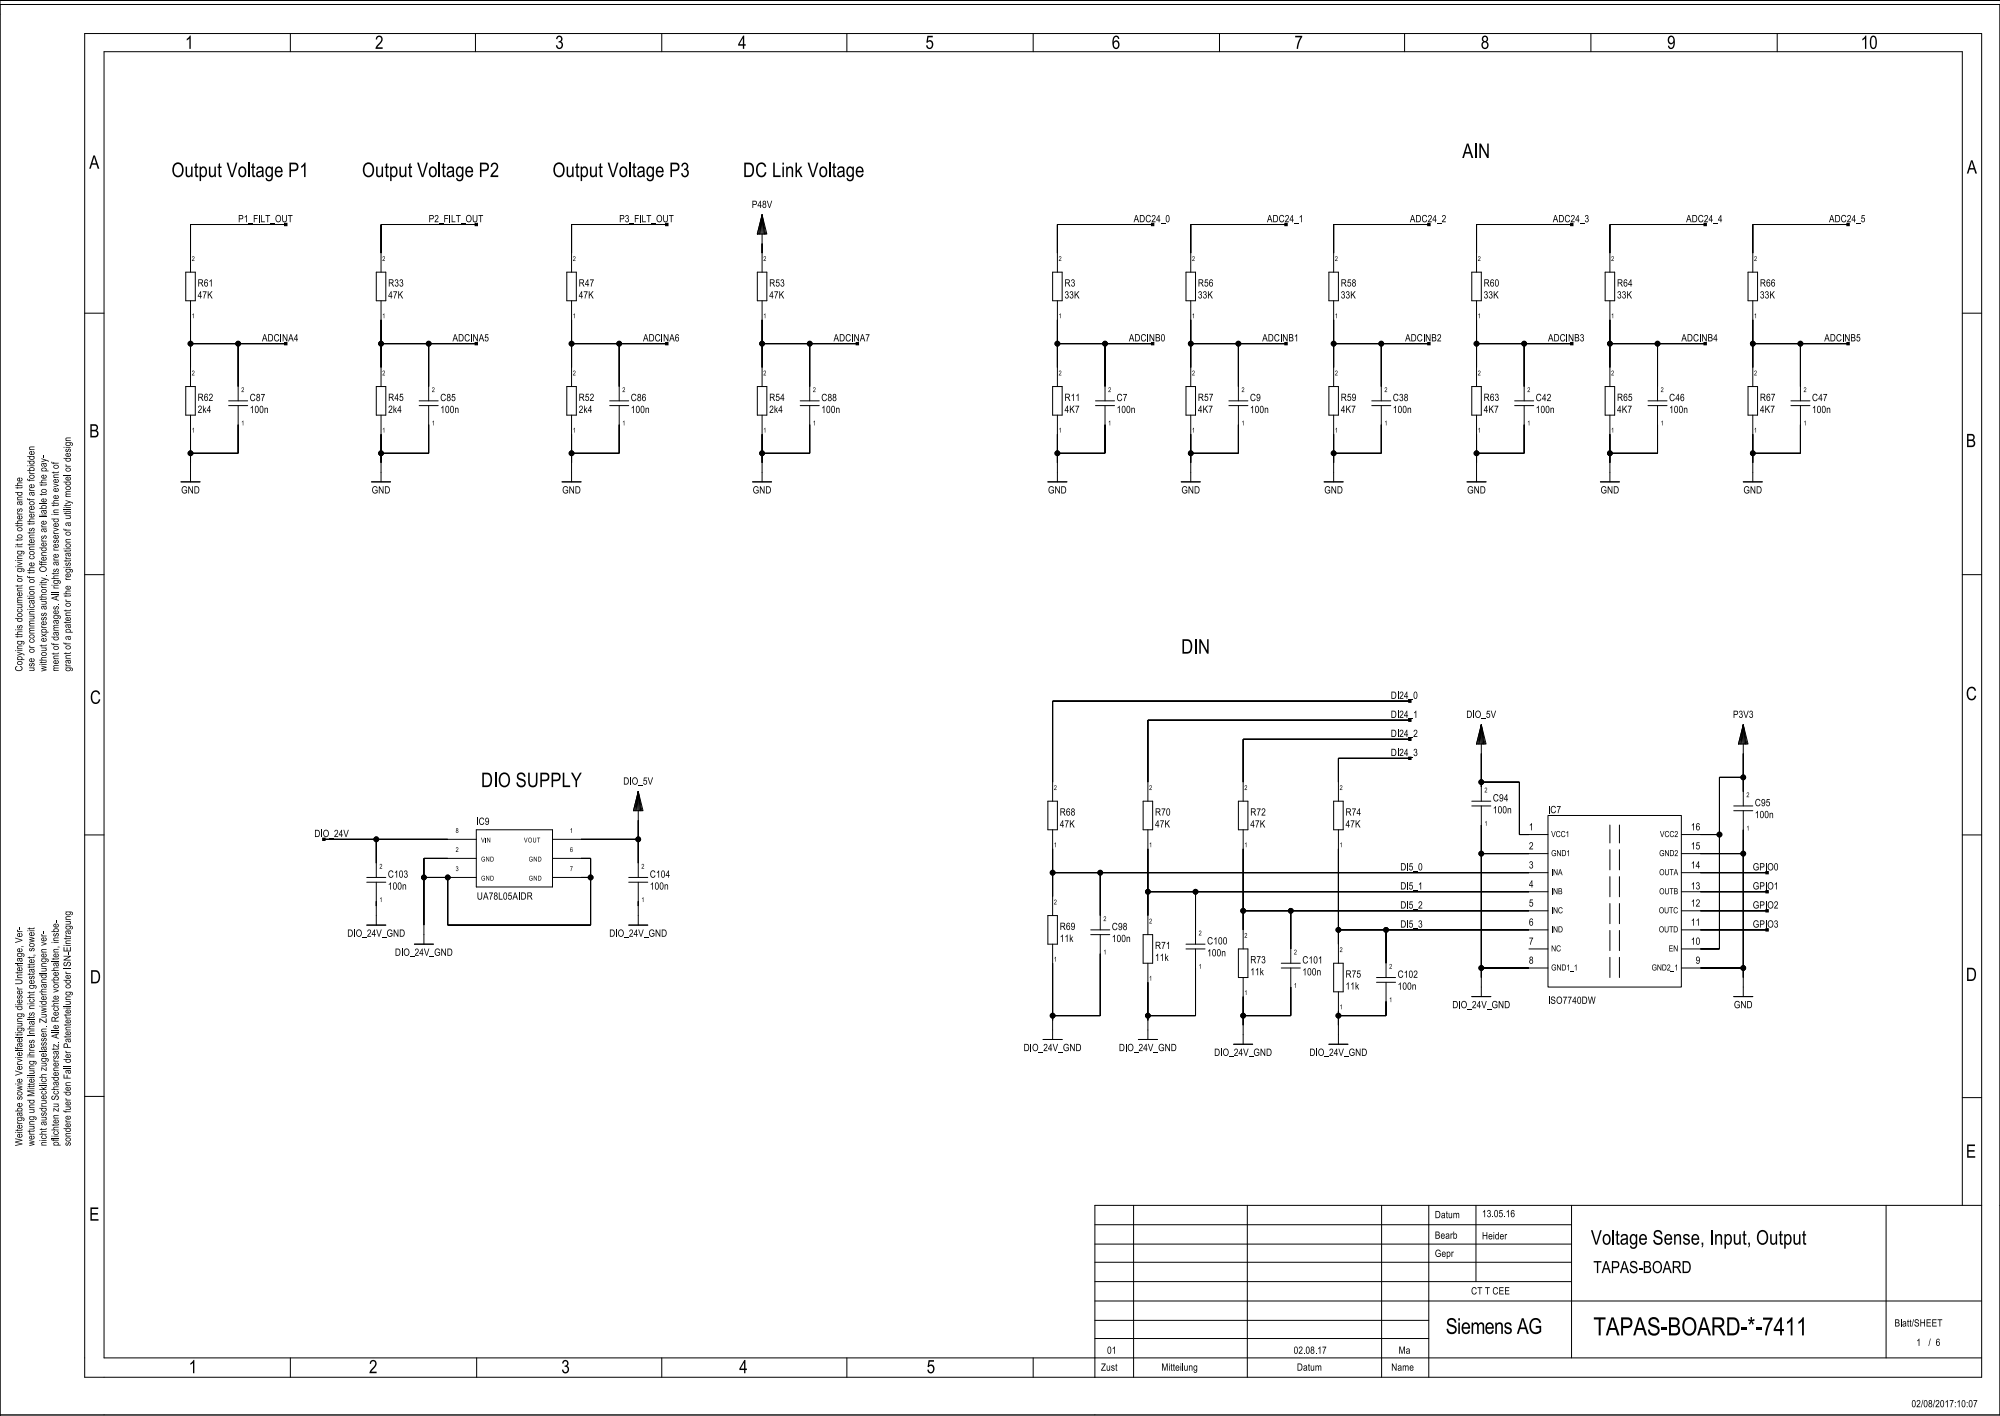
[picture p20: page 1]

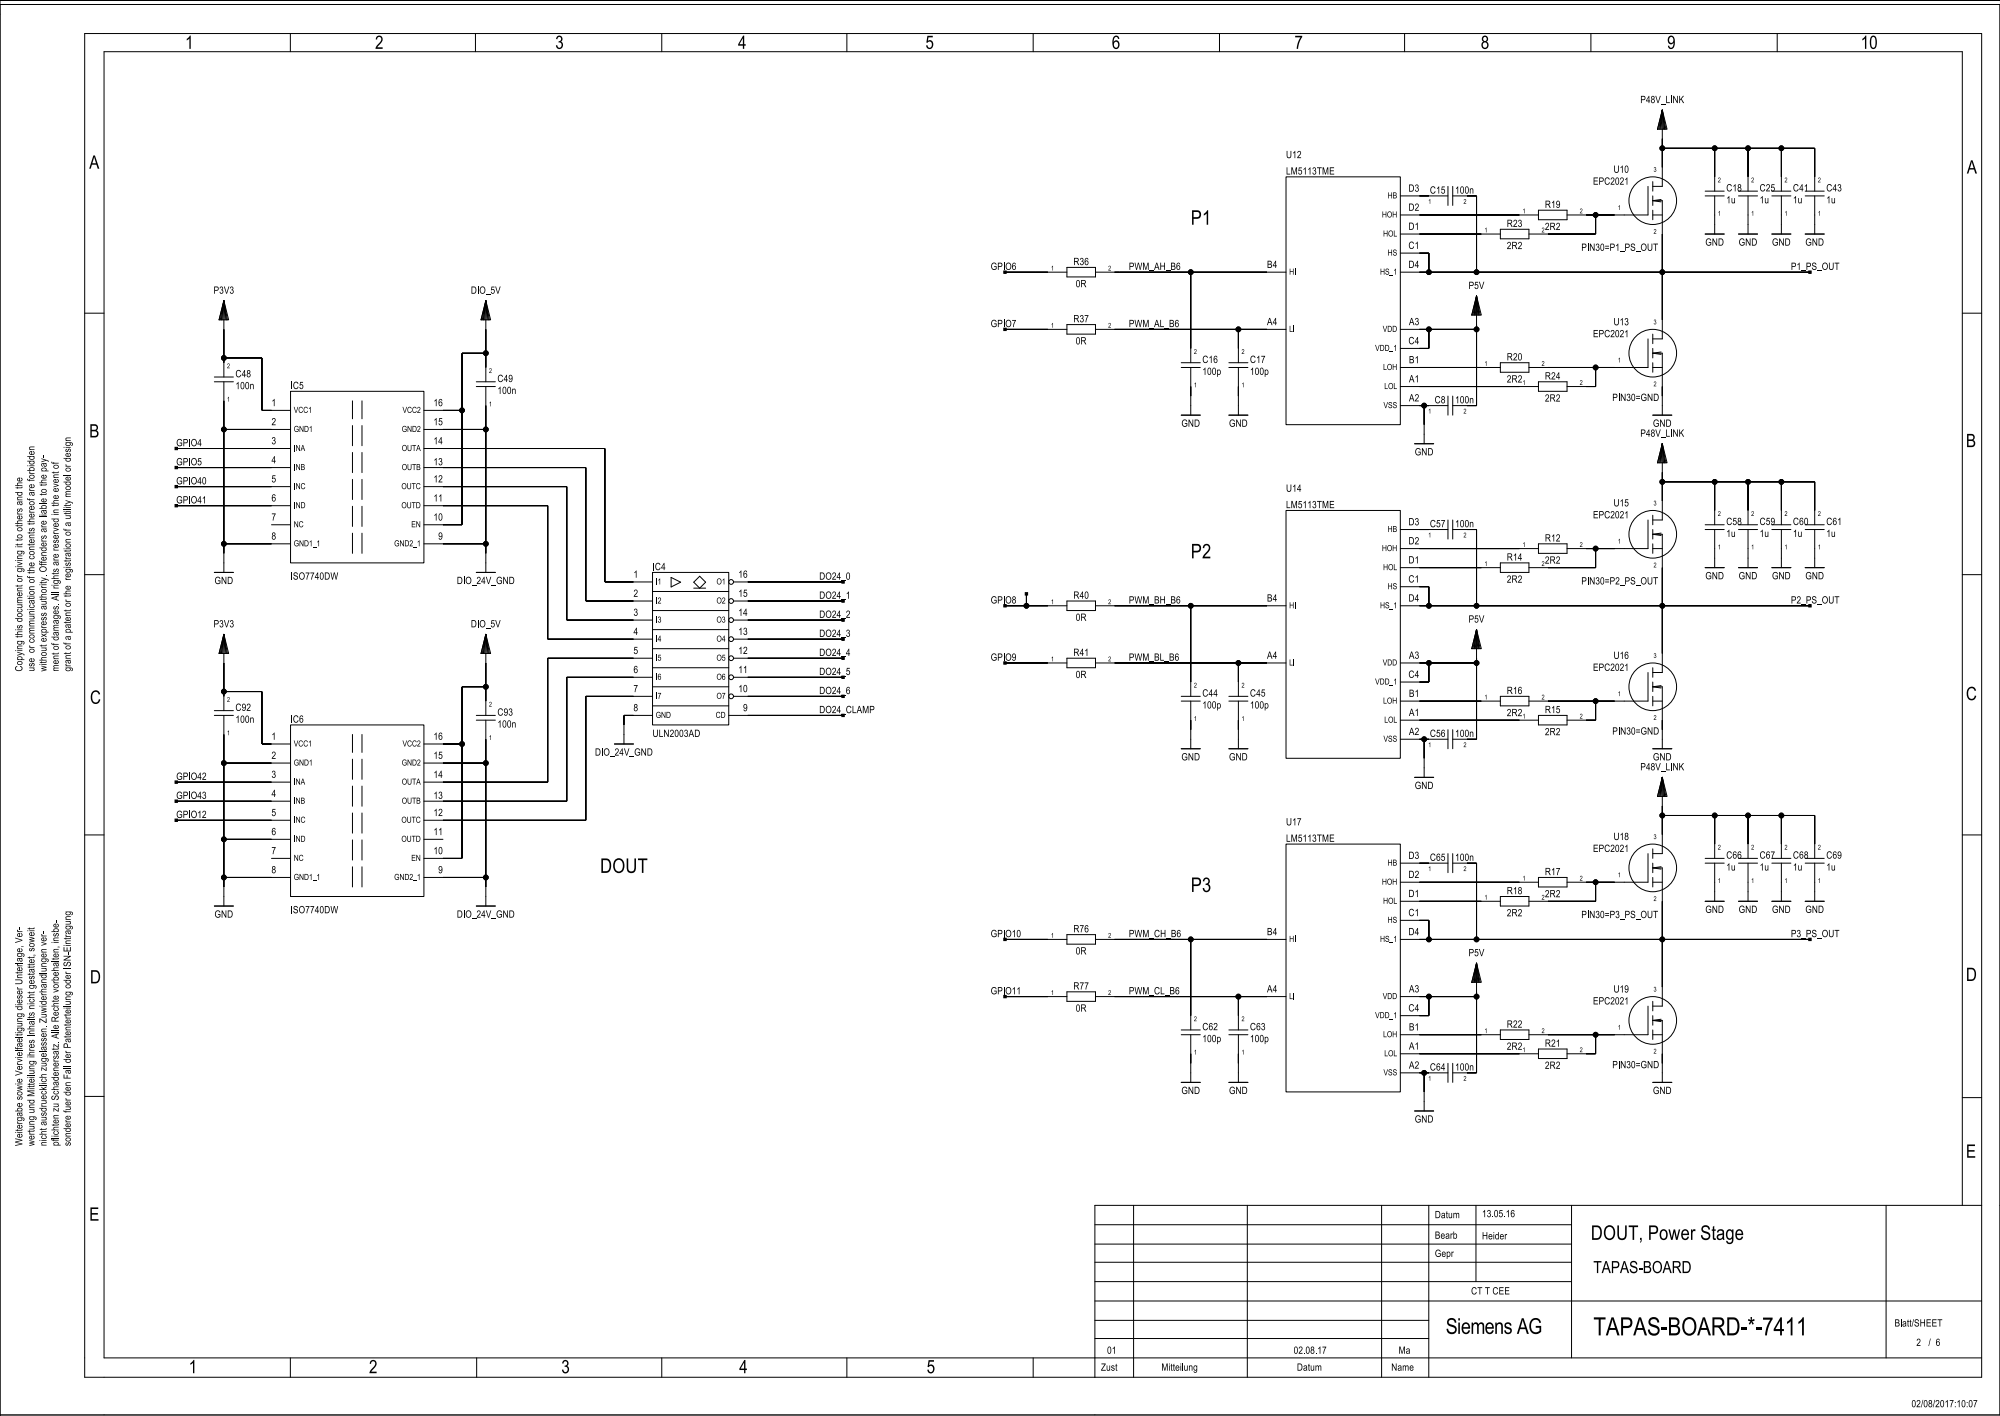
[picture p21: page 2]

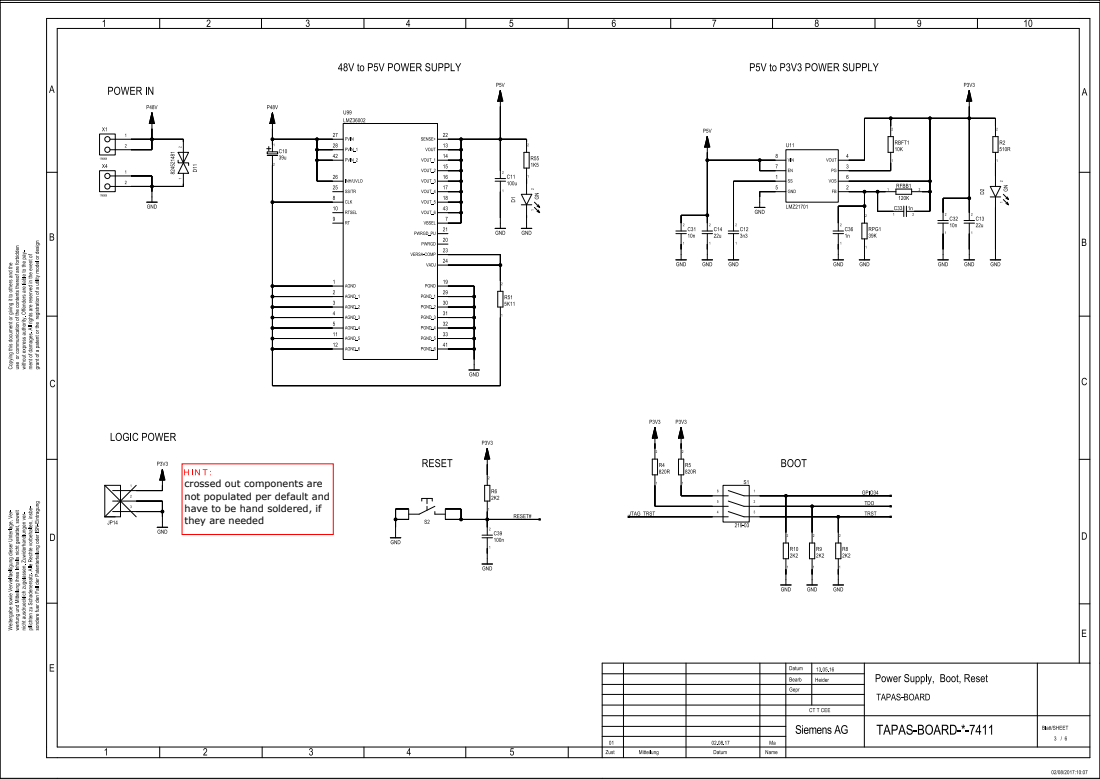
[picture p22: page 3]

crossed out components are
not populated per default and
have to be hand soldered, if
they are needed

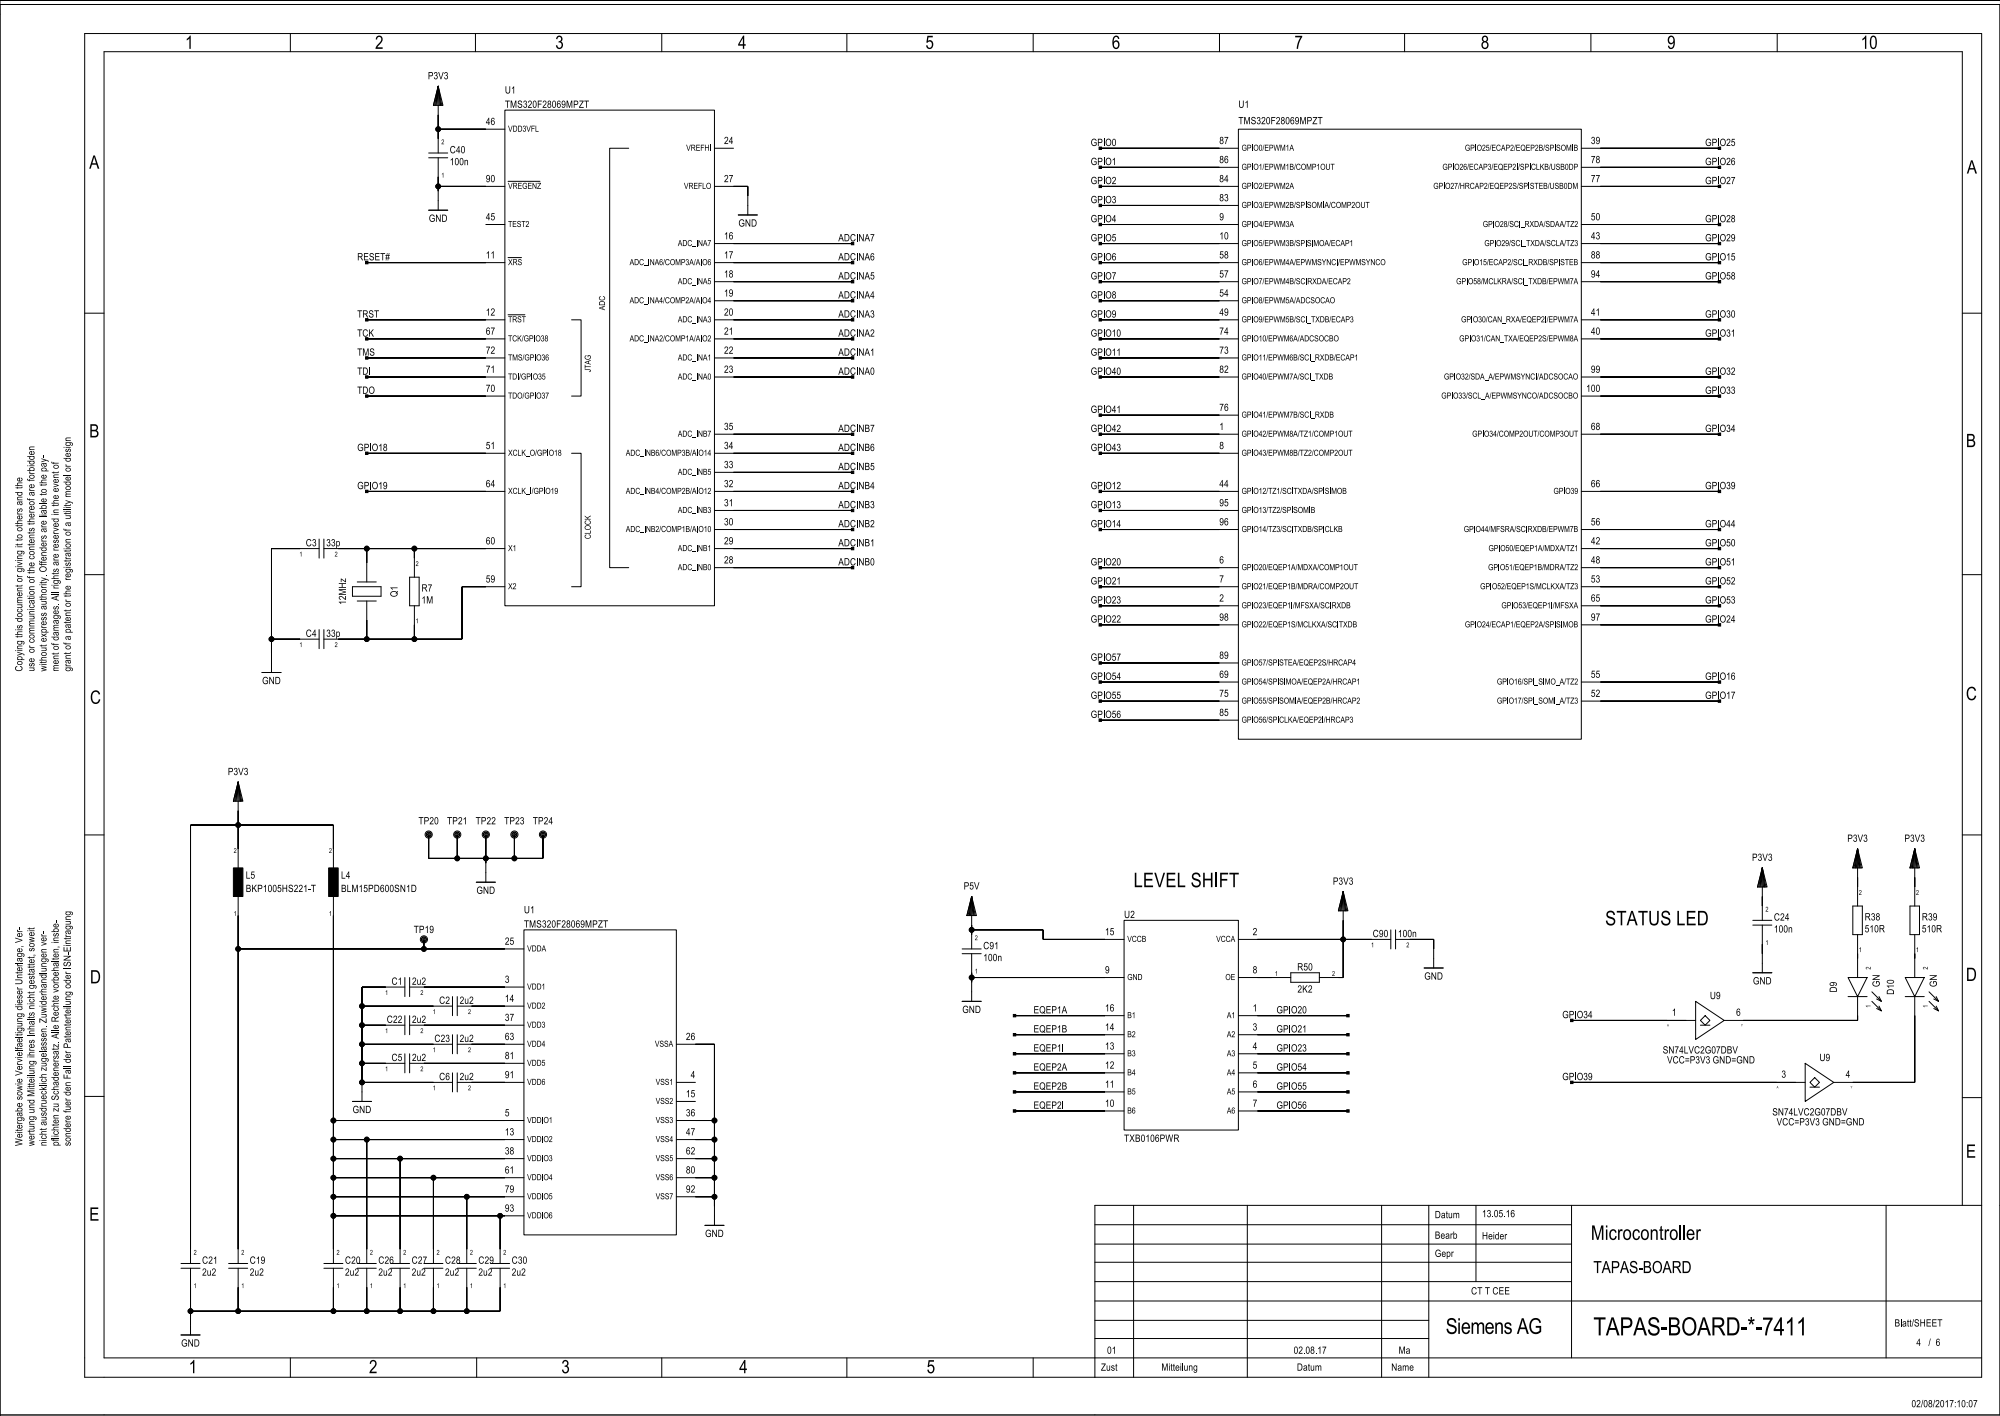
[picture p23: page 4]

A
A

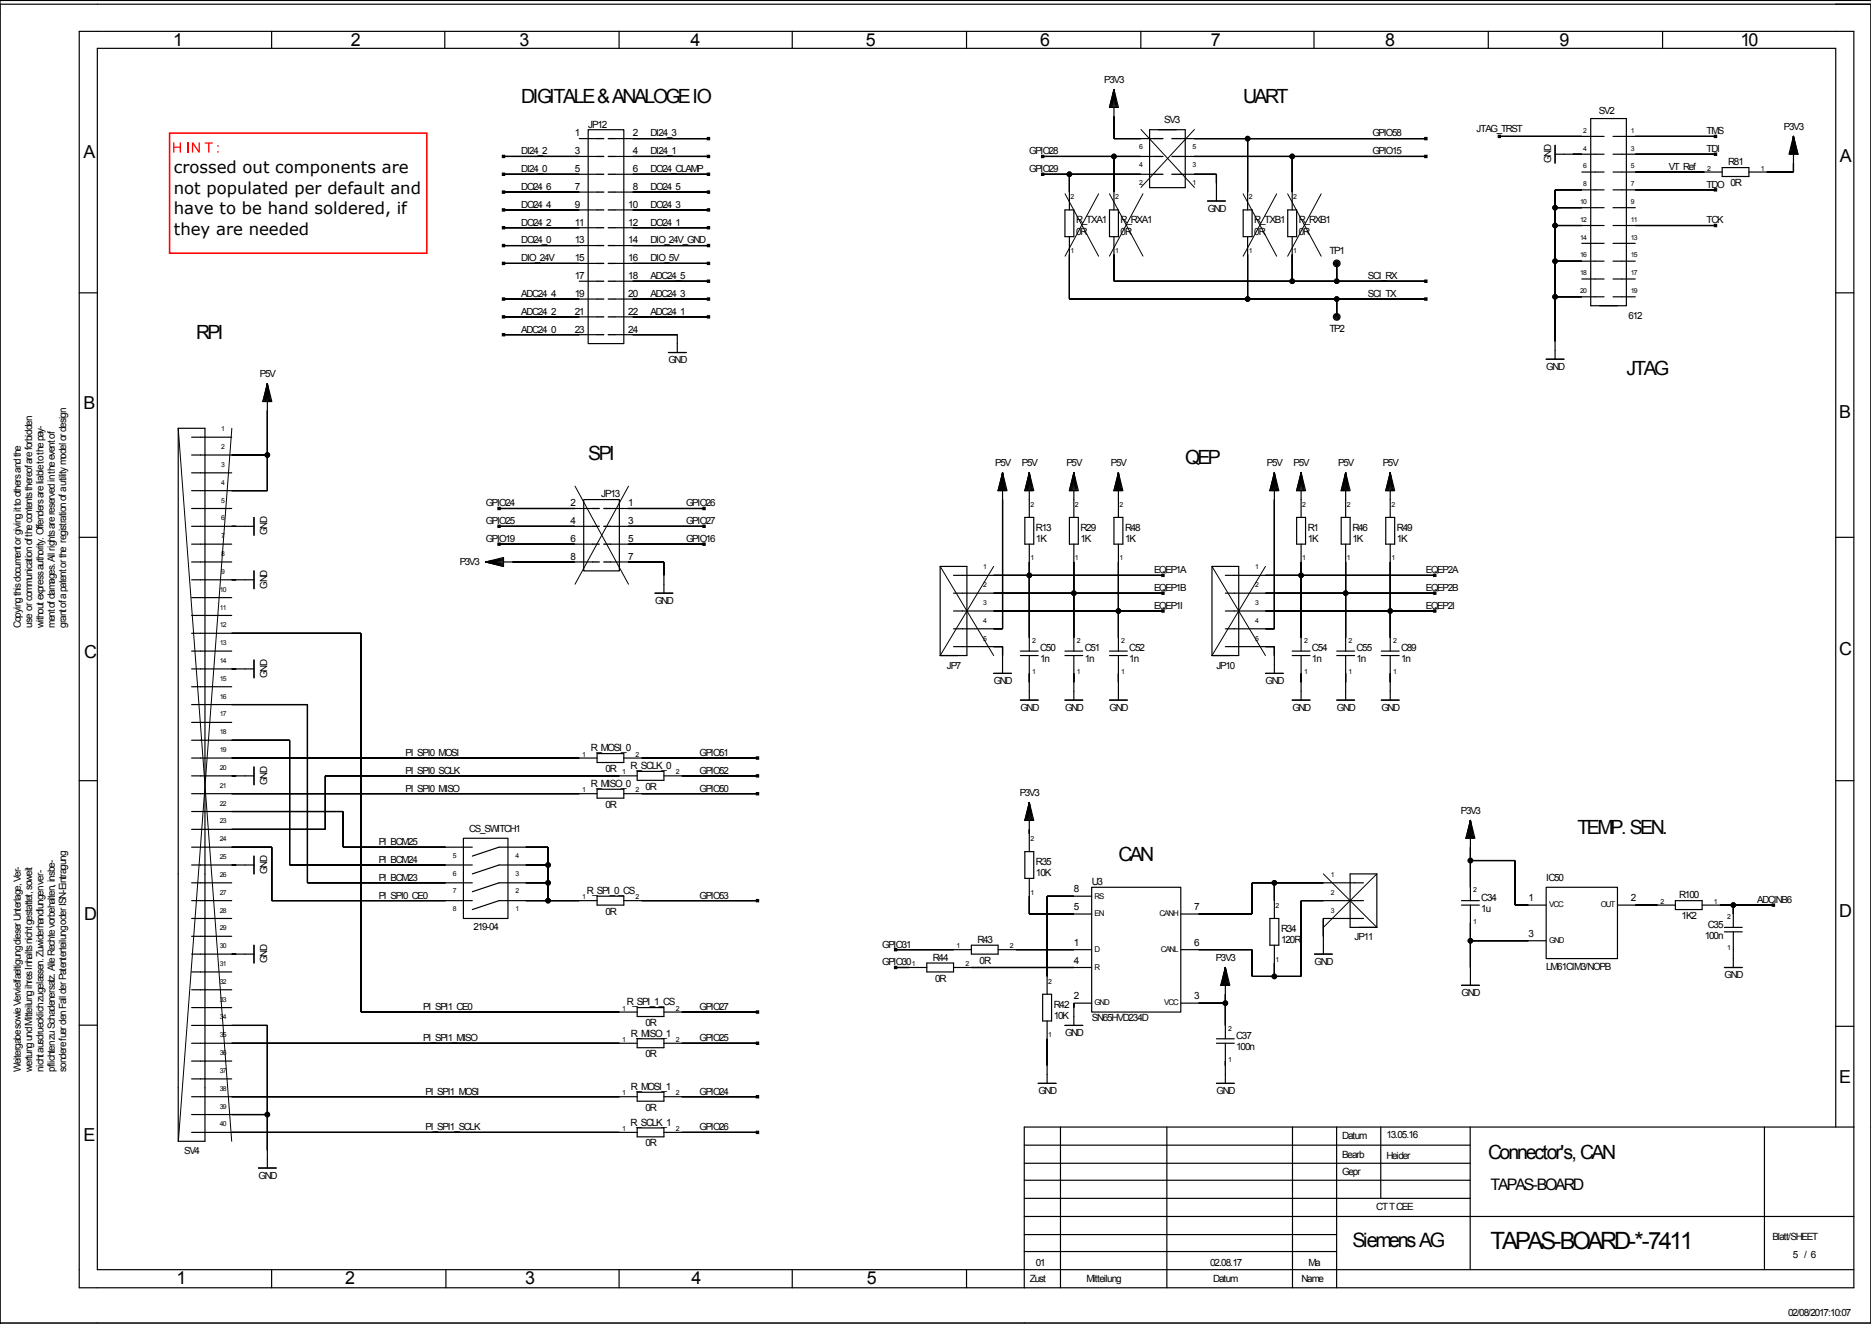
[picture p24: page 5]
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

grant of a patent or the registration of a utility model or design

use or communication of the contents thereof are forbidden

without express authority. Offenders are liable to the pay-

ment of damages. All rights are reserved in the event of

Copying this document or giving it to others and the

GND GND GND

pflichten zu Schadenersatz. Alle Rechte vorbehalten, insbe-

sondere fuer den Fall der Patenterteilung oder ISN-Eintragung

Weitergabe sowie Vervielfaeltigung dieser Unterlage, Ver-

wertung und Mitteilung ihres Inhalts nicht gestattet, soweit

nicht ausdruecklich zugelassen. Zuwiderhandlungen ver-

Datum | 13.05.16 | Connector's, CAN TAPAS-BOARD
Bearb | Heider
Gepr

CT T CEE

Siemens AG | TAPAS-BOARD-*-7411 | Blatt/SHEET 5 / 6

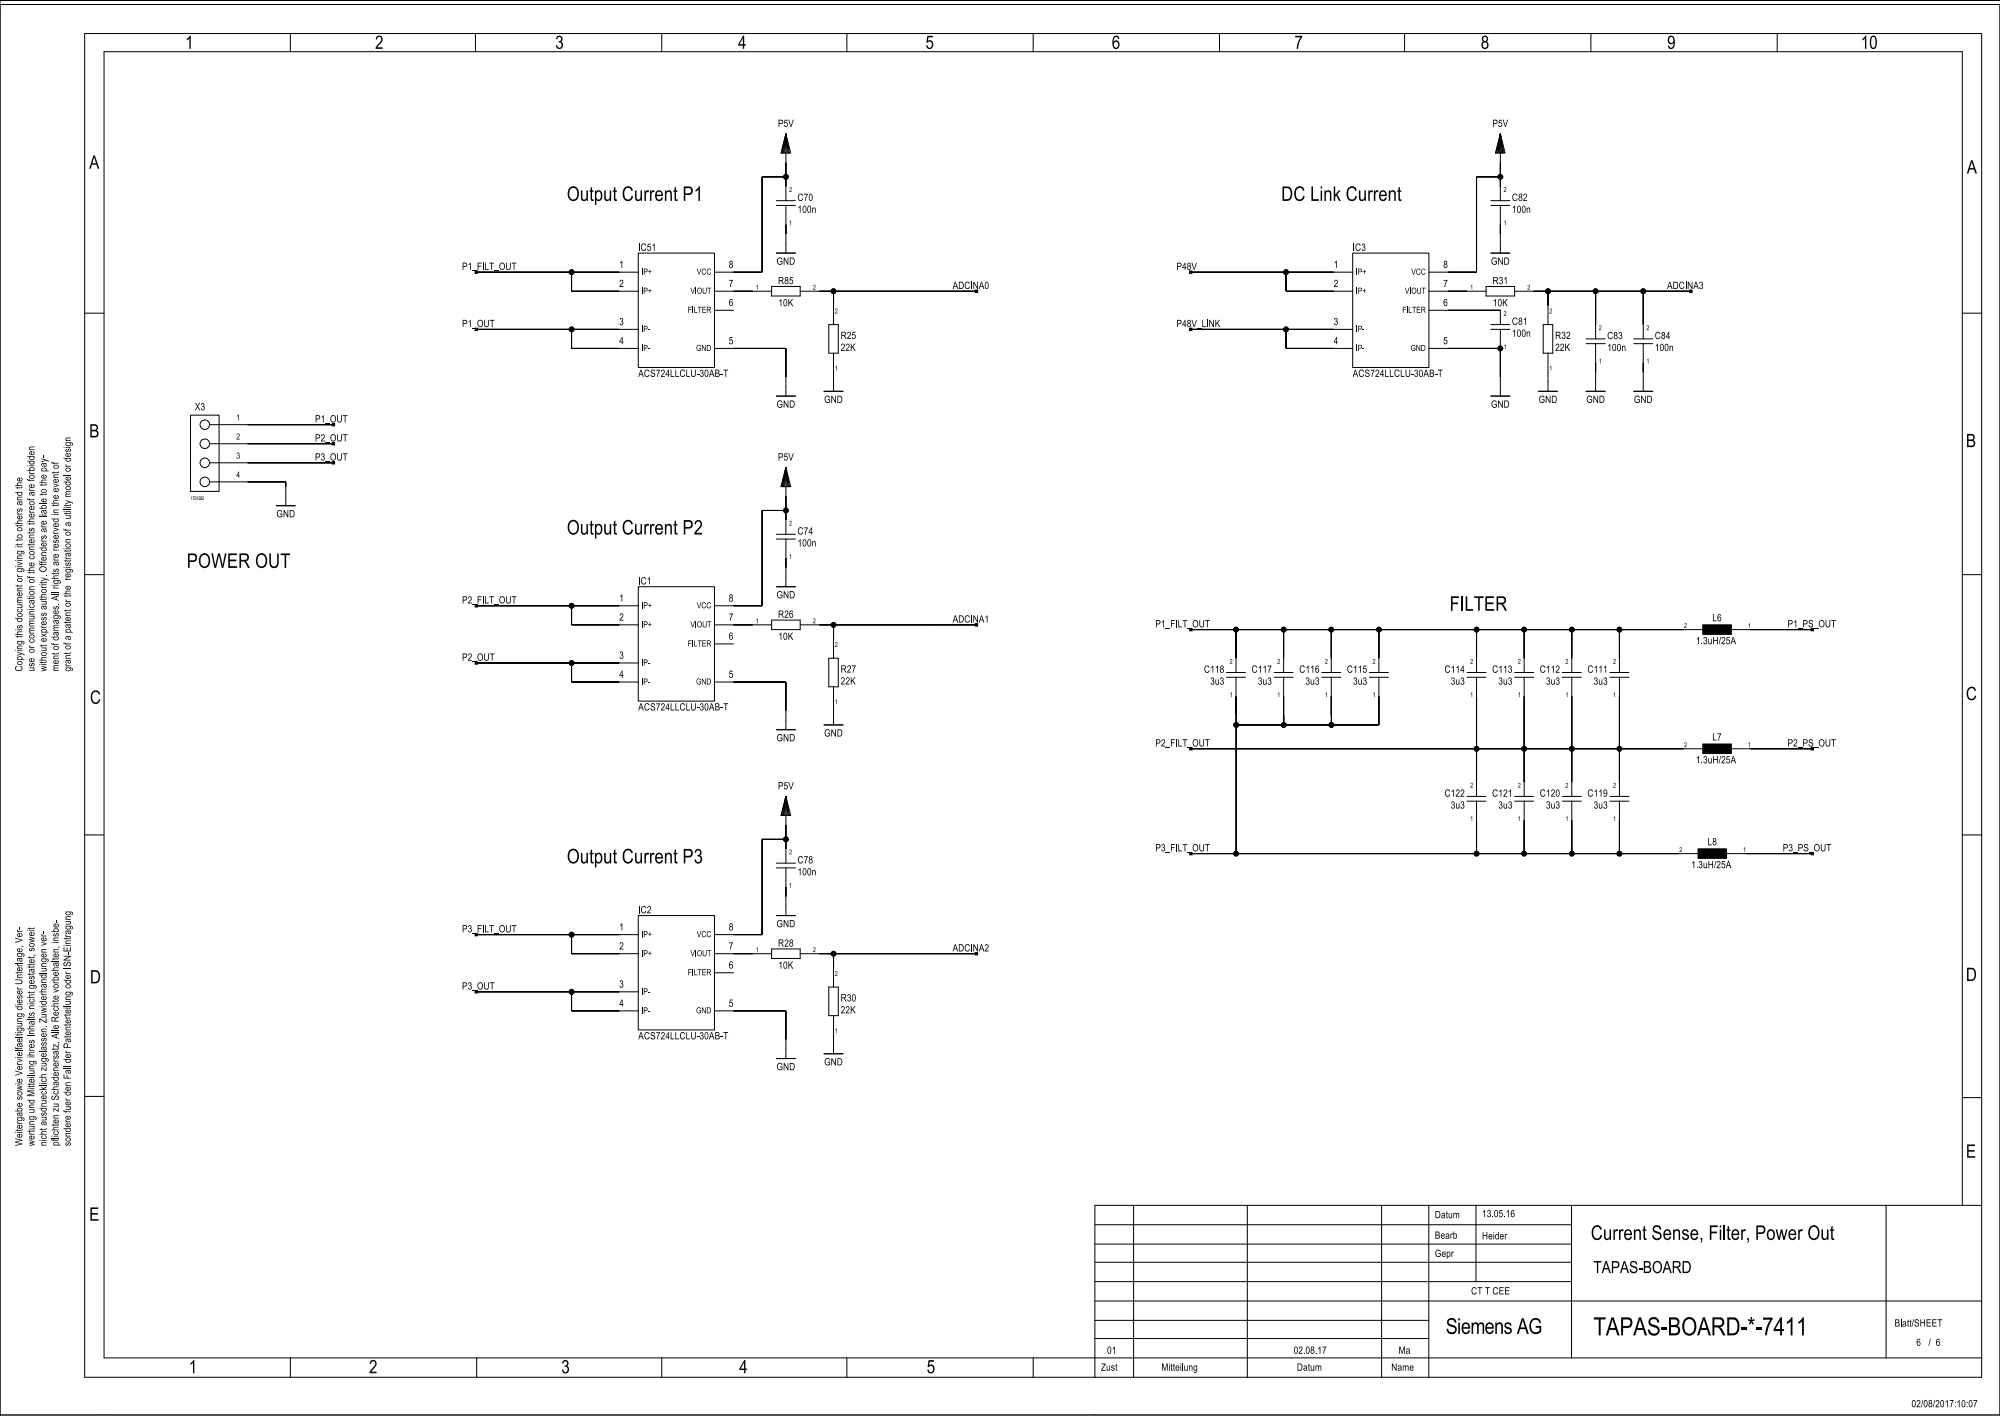
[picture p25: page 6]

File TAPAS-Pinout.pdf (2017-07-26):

## JTAG - Interface

Digital and Analog IO GND A¹ In A³ In A5 In DIO ⁵V Out DIO GND D¹ Out D³ Out D⁵ Out DOut Clamp

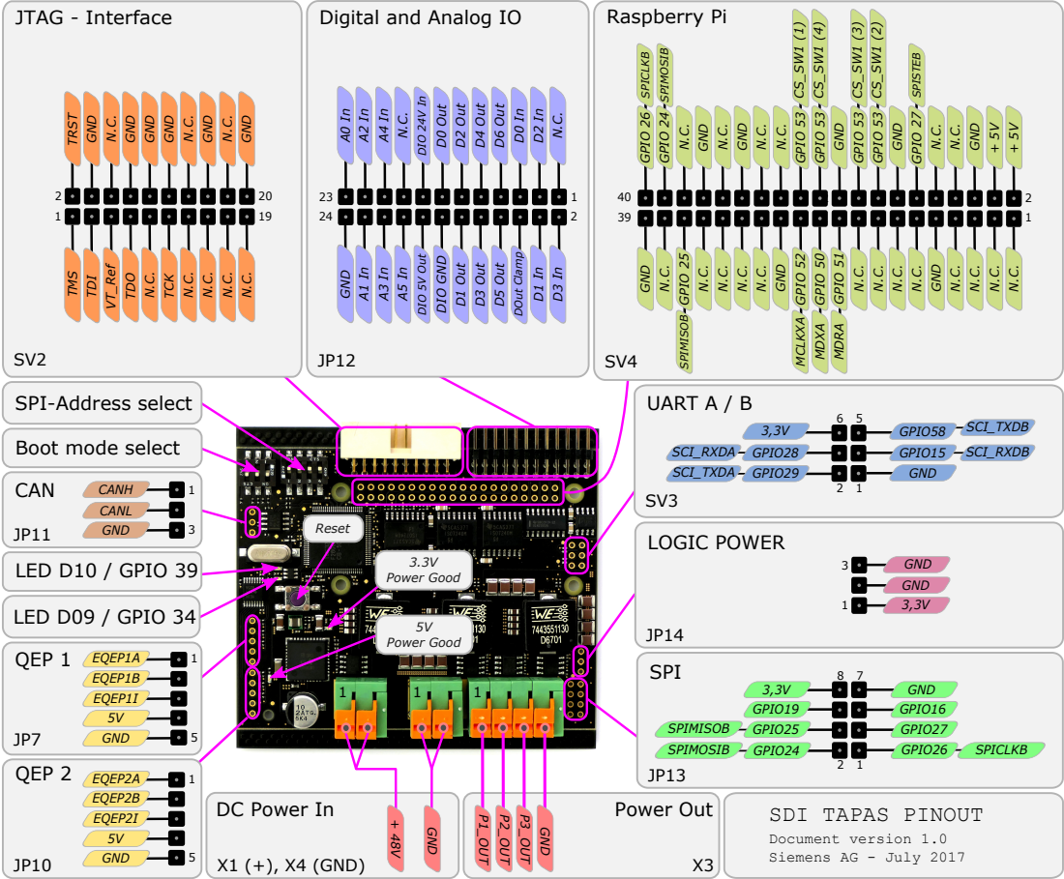
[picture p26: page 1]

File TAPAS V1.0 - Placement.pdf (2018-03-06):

A

B

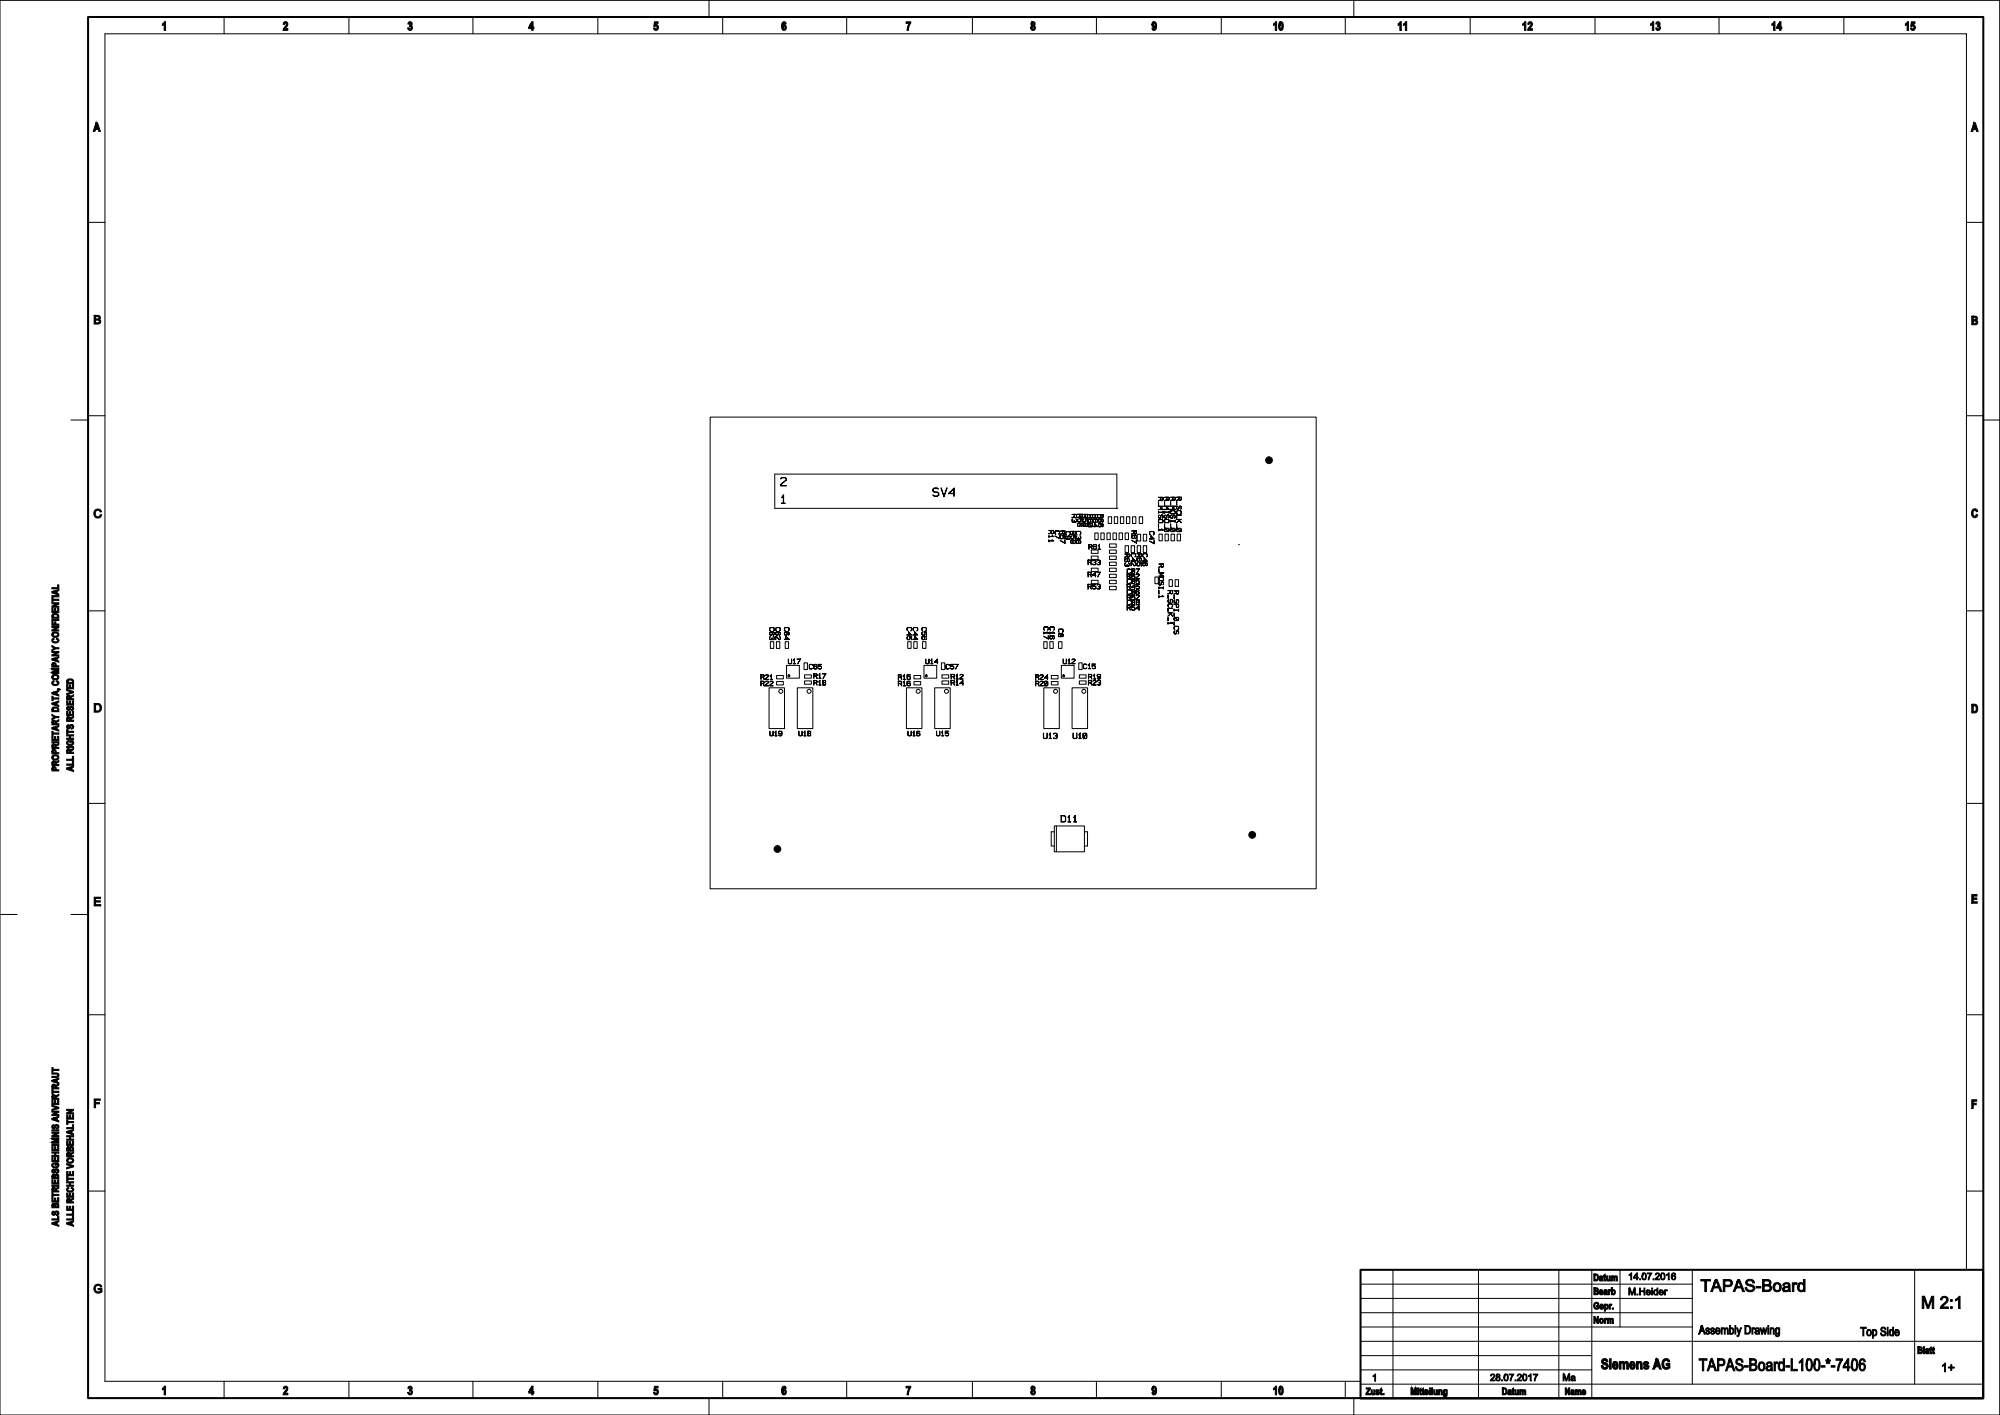
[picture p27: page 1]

PROPRIETARY DATA, COMPANY CONFIDENTIAL

A

B

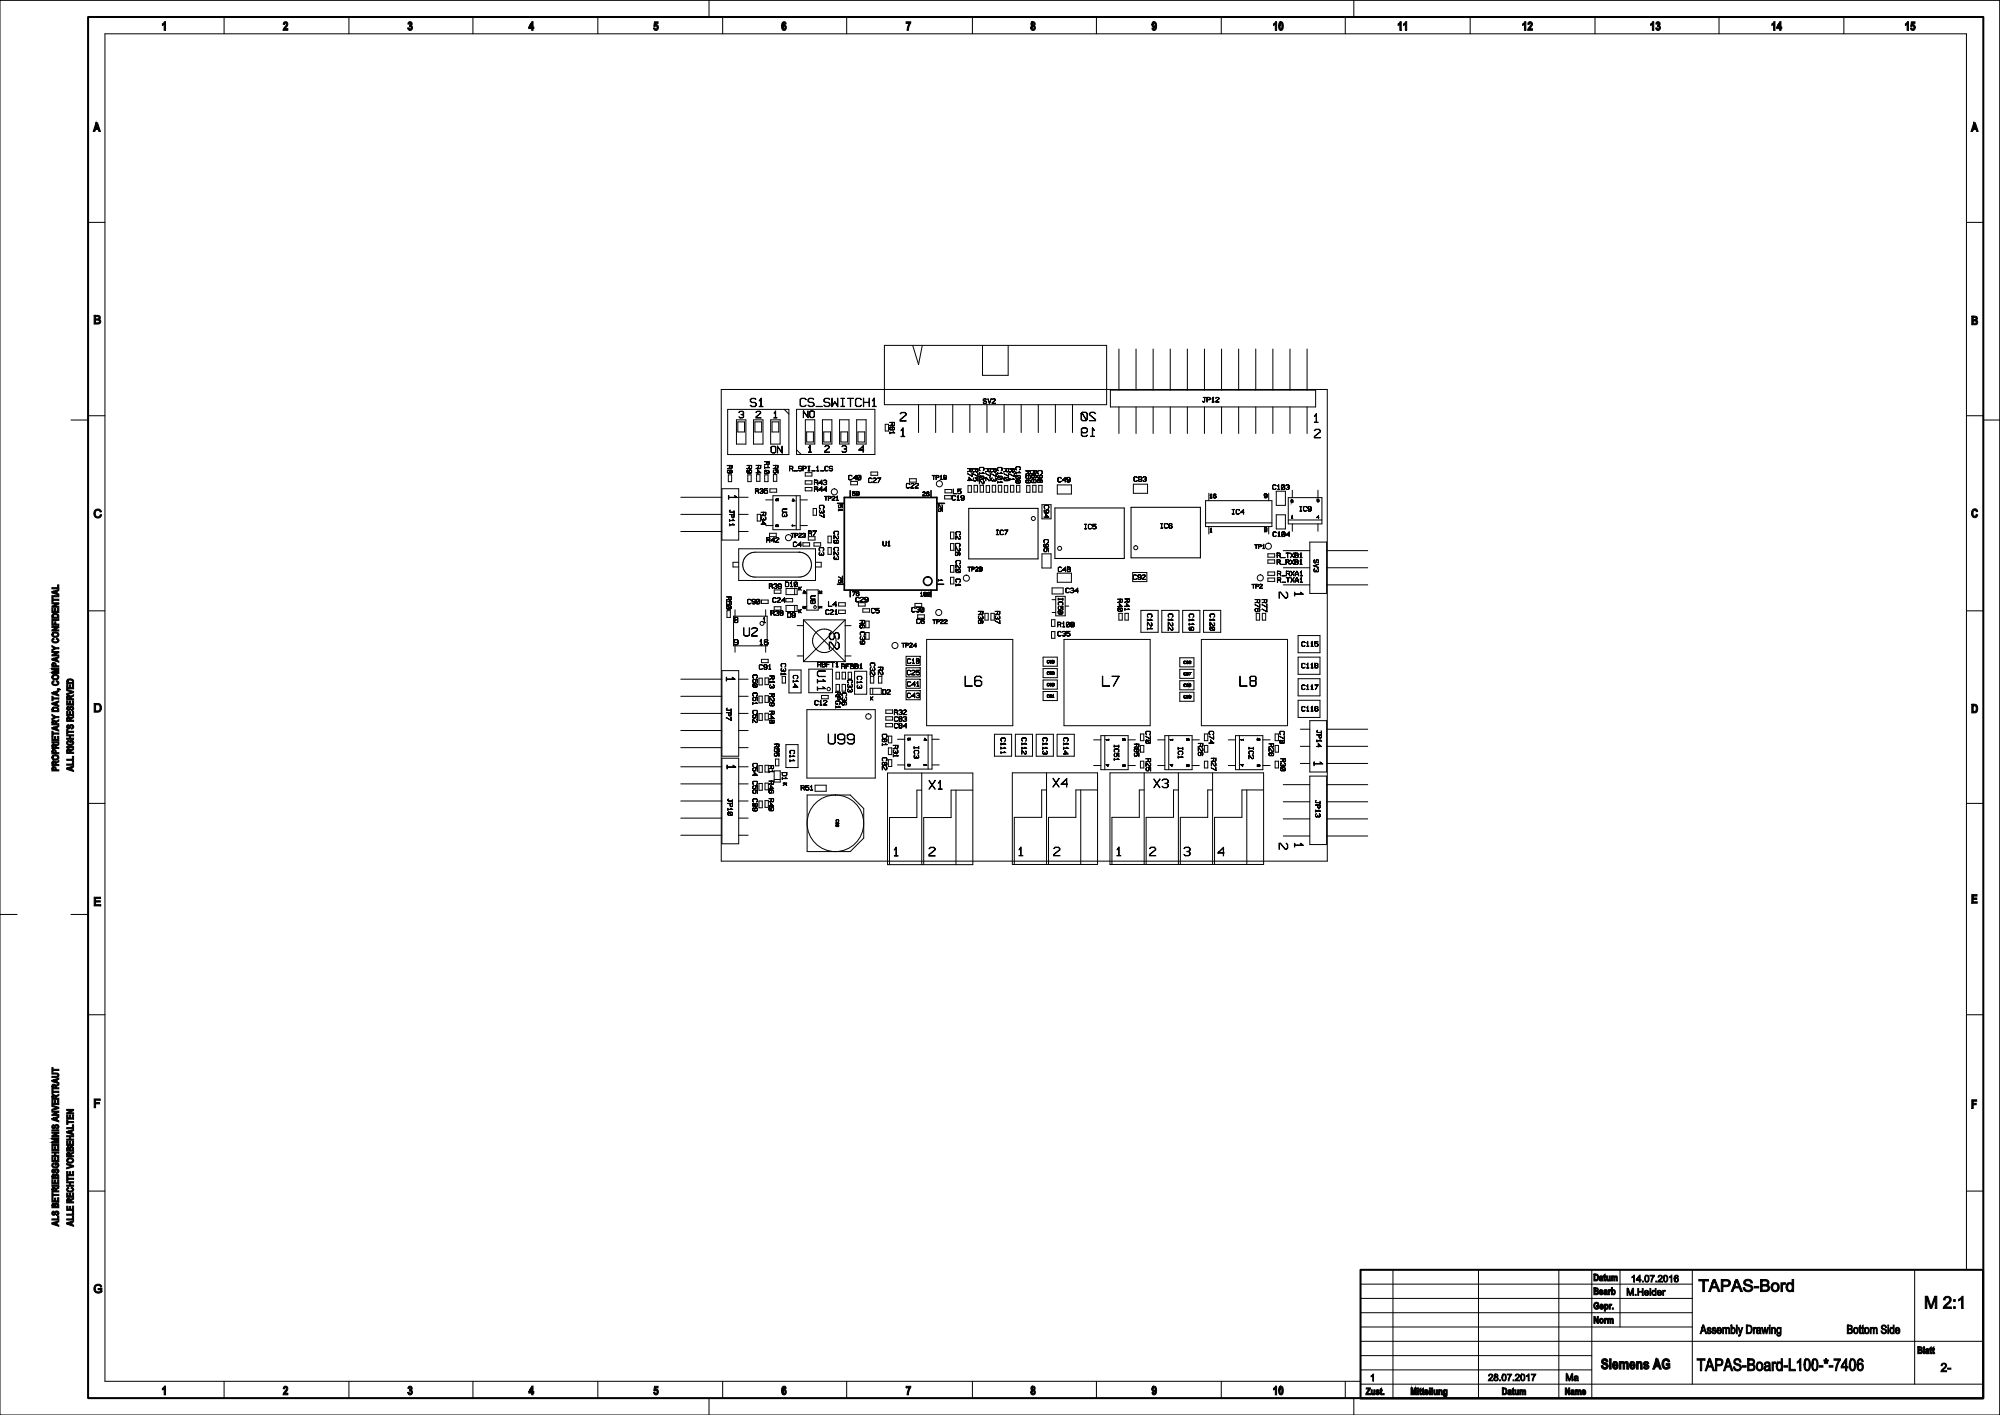
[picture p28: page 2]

PROPRIETARY DATA, COMPANY CONFIDENTIAL

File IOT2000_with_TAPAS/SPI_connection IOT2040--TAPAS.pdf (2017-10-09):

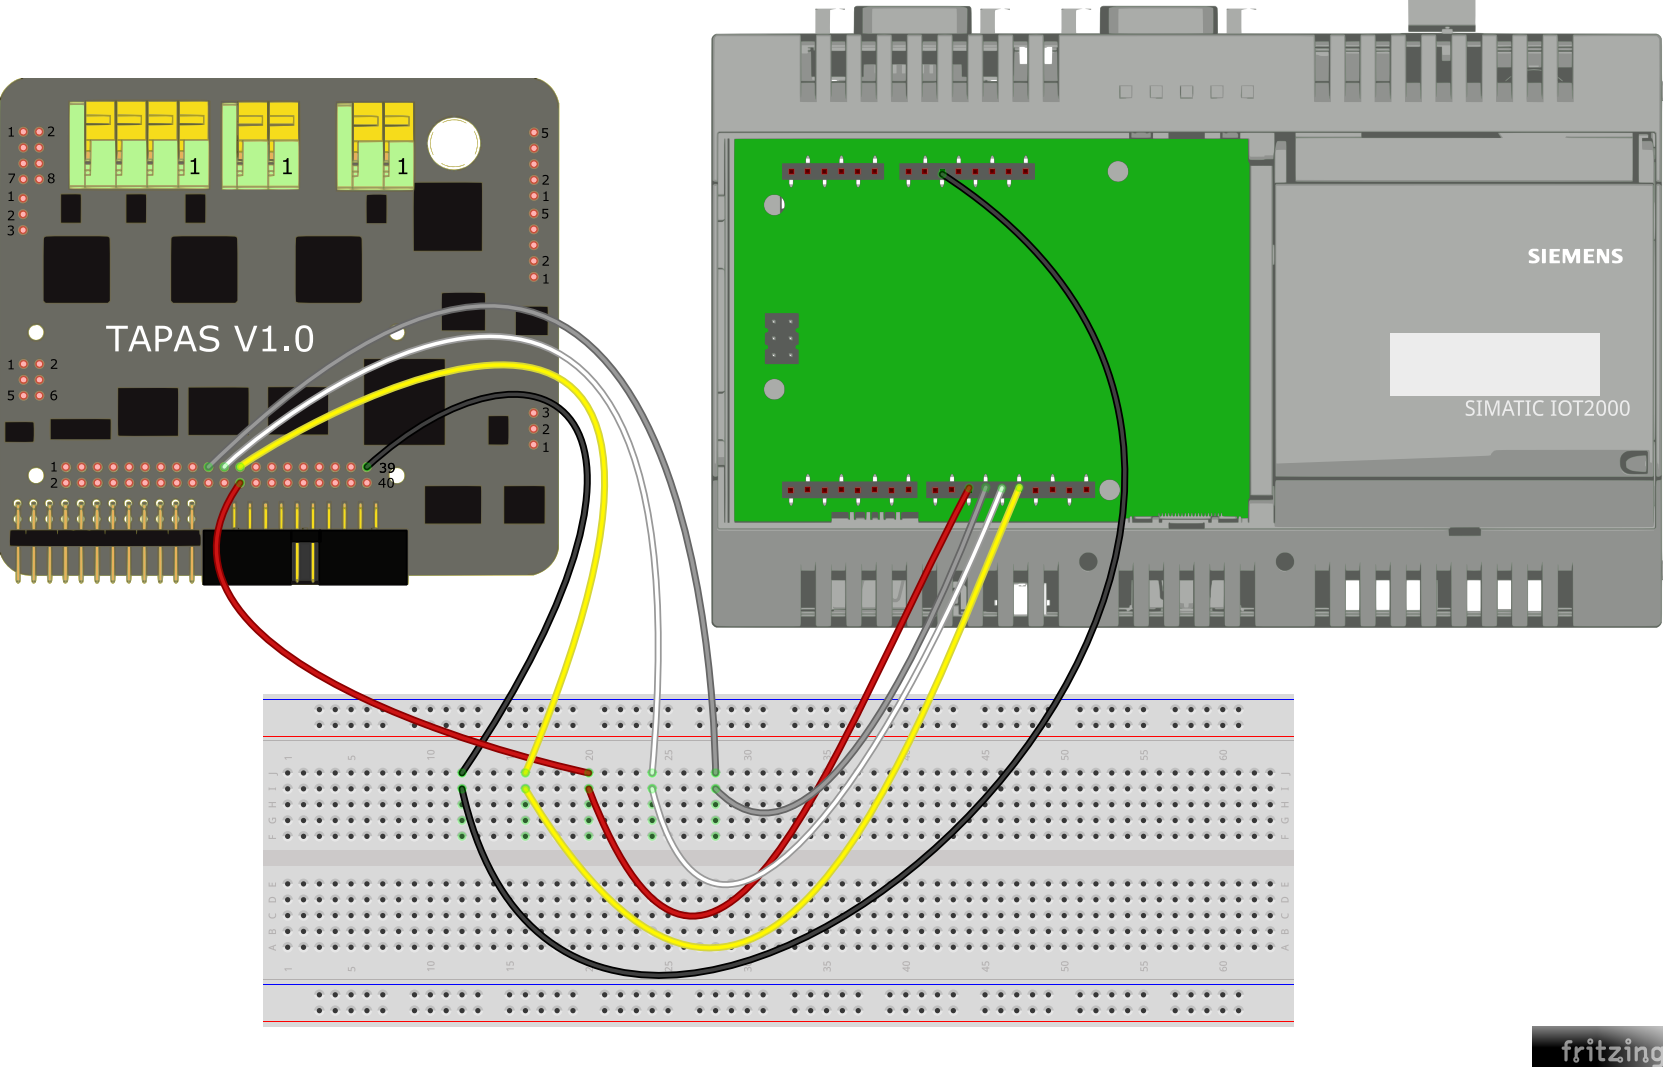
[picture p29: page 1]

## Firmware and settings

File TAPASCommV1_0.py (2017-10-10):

###################################################################################################
## SDI TAPAS python demo application - communication module
## 
## Revisions:
## 1.0 - Initial version
## 
## Copyright (c) 2017 Siemens AG
# Redistribution and use in source and binary forms, with or without 
# modification, are permitted provided that the following conditions 
# are met:
#
# 1. Redistributions of source code must retain the above copyright 
#    notice, this list of conditions and the following disclaimer. 
#
# 2. Redistributions in binary form must reproduce the above copyright   
#    notice, this list of conditions and the following disclaimer in the
#    documentation and/or other materials provided with the distribution.
#
# 3. Neither the name of the copyright holder nor the names of 
#    its contributors may be used to endorse or promote products derived 
#    from this software without specific prior written permission.
#
# THIS SOFTWARE IS PROVIDED BY THE COPYRIGHT HOLDERS AND CONTRIBUTORS "AS IS"
# AND ANY EXPRESS OR IMPLIED WARRANTIES, INCLUDING, BUT NOT LIMITED TO,
# THE IMPLIED WARRANTIES OF MERCHANTABILITY AND FITNESS FOR A PARTICULAR
# PURPOSE ARE DISCLAIMED. IN NO EVENT SHALL THE COPYRIGHT HOLDER OR
# CONTRIBUTORS BE LIABLE FOR ANY DIRECT, INDIRECT, INCIDENTAL, SPECIAL, 
# EXEMPLARY, OR CONSEQUENTIAL DAMAGES (INCLUDING, BUT NOT LIMITED TO,
# PROCUREMENT OF SUBSTITUTE GOODS OR SERVICES; LOSS OF USE, DATA, OR PROFITS;
# OR BUSINESS INTERRUPTION) HOWEVER CAUSED AND ON ANY THEORY OF LIABILITY,
# WHETHER IN CONTRACT, STRICT LIABILITY, OR TORT (INCLUDING NEGLIGENCE OR 
# OTHERWISE) ARISING IN ANY WAY OUT OF THE USE OF THIS SOFTWARE, 
# EVEN IF ADVISED OF THE POSSIBILITY OF SUCH DAMAGE.
###################################################################################################

# module for platform check
import platform
                     
# module for data handling
import struct

# global variable necessary for crc-calculation
crc_table = [0] * 256

# used for crc
POLY = 0x1021
START = 0xFFFF
###
if (platform.machine() == "i586"):
    # this is necessary to run the script on IOT2000
    # (manual control of the CS-pin)
    #set filename for set_chipselect
    CS = "/sys/class/gpio/gpio10/value"

#function for setting chipselect, necessary only on IOT2000
def set_chipselect (status):
    file = open(CS, 'w')

    if(status == 0):
        file.write("0")
    elif(status == 1):
        file.write("1")
    else:
        file.write("0")

    file.close()
###

def GenerateCrcTable():
	for i in range(0, 256, 1):
		crc = i << 8
		for j in range(0, 8, 1):
			if crc & 0x8000:
				crc <<= 1
				crc = crc ^ POLY 
			else:
				crc <<= 1
		crc_table[i] = crc & 0xFFFF # just regard the lower 16Bit of the value

def CalcCrc(data, len_words):
	crc = START
	for i in range(0, len_words, 1):
		octet = data[i] & 0xFF

		idx = ((crc >> 8) & 0xFF) ^ octet
		crc = (crc << 8) ^ crc_table[idx]
		
		octet = (data[i] >> 8) & 0xFF
		idx = ((crc >> 8) & 0xFF) ^ octet
		crc = (crc << 8) ^ crc_table[idx]
	crc = crc & 0xFFFF # just regard the lower 16Bit of the value
	return crc

def transferMasterSlave(spi,flags, numPolePairs, ratedCurrent,
                        RoverLestFrequency, fluxEstFrequency,
                        setpointSpeed, setpointAccel):
 
    # packing data together
    sender_temp = struct.pack('HHffffffffffffffffHHHH', flags, numPolePairs, ratedCurrent, RoverLestFrequency, fluxEstFrequency, setpointSpeed, setpointAccel,
                0.0,0.0,0.0,0.0,0.0,0.0,0.0,0.0,0.0,0.0,0.0, 0, 0, 0, 0)
    sender = []
    sender16 = []

    # first create a list containing all the single Bytes 
    for byte in sender_temp:
        sender.append(byte)

    # then create a second list which holds 16Bit values and the bytes swapped
    for i in range(0, len(sender), 2):
        temp = (sender[i+1]<<8) | (sender[i] )
        sender16.append(temp)

    # calculate the checksum for the "package" to be sent   
    send_CRC = CalcCrc(sender16, ((len(sender)//2)-1))
    packed_CRC = struct.pack('H', send_CRC)

    # now, add the Checksum to the package to be sent 
    sender[len(sender)-2] = packed_CRC[0]
    sender[len(sender)-1] = packed_CRC[1]

    resp = []
    receiver = []

    for i in range(0, len(sender), 2):
        ### 
        # IOT2000 : necessary to set and reset the CS-Pin by hand
        if (platform.machine() == "i586"):
            set_chipselect(0)
        ###

        res2 = spi.xfer( [sender[i+1], sender[i]], 20000)
        
        ###
        # IOT2000 : manually drive CS back
        if (platform.machine() == "i586"):
            set_chipselect(1) 
        ###

        resp.append(res2[1])
        resp.append(res2[0])

    resp_bytes = struct.pack('B'*len(resp), *resp)
    resp_calcCrc = struct.unpack('H'*((len(resp_bytes)//2)), resp_bytes)
    resp_readable = struct.unpack('HHffffHHfffffffffffHHHH', resp_bytes)

    for byte in resp_calcCrc:
        receiver.append(byte)

    recv_CRC = CalcCrc(receiver, (len(receiver)-1))

    if(recv_CRC == int(resp_readable[22])):
        SPIstatus = 1
    else:
        SPIstatus = 0

    resp_readable = resp_readable + (SPIstatus,)
    slave_rx_dict={};
    slave_rx_dict["flags"] = resp_readable[0]
    slave_rx_dict["Protection mode"] = resp_readable[1]
    slave_rx_dict["dc-bus voltage"] = resp_readable[2]
    slave_rx_dict["dc-bus current"] = resp_readable[3]
    slave_rx_dict["board-temperature"] = resp_readable[4]
    slave_rx_dict["motor speed"] = resp_readable[5]
    slave_rx_dict["controller state [CTRL_state]"] = resp_readable[6]
    slave_rx_dict["estimator state [EST_state]"] = resp_readable[7]
    slave_rx_dict["motorRs"] = resp_readable[8]
    slave_rx_dict["motorRr"] = resp_readable[9]
    slave_rx_dict["motorLsd"] = resp_readable[10]
    slave_rx_dict["motorLsq"] = resp_readable[11]
    slave_rx_dict["ratedFlux"] = resp_readable[12]
    slave_rx_dict["analog in 0 voltage"] = resp_readable[13]
    slave_rx_dict["analog in 1 voltage"] = resp_readable[14]
    slave_rx_dict["analog in 2 voltage"] = resp_readable[15]
    slave_rx_dict["analog in 3 voltage"] = resp_readable[16]
    slave_rx_dict["analog in 4 voltage"] = resp_readable[17]
    slave_rx_dict["analog in 5 voltage"] = resp_readable[18]
    slave_rx_dict["status digital inputs"] = resp_readable[19]
    slave_rx_dict["spi status slave"] = resp_readable[20]
    slave_rx_dict["reserved2"] = resp_readable[21]
    slave_rx_dict["CRC"] = resp_readable[22]
    slave_rx_dict["spi connection status"] = SPIstatus
    return slave_rx_dict

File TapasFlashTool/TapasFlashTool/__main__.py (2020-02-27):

"""
TapasFlashTool -- This script can be used to flash a TapasBoard using the UART interface.

Author: Stefan Steinmueller

BSD 3-Clause License

Copyright (c) 2017, SDI-SoftwareDefinedInverter
All rights reserved.

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
* Neither the name of the copyright holder nor the names of its
  contributors may be used to endorse or promote products derived from
  this software without specific prior written permission.

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
import time
import argparse
import sys
import logging
import os
import time
import pdb
# not standard
import progressbar
import serial as serial
start_time = time.time()
parser = argparse.ArgumentParser()
parser.add_argument("-b", default=9600, help="Set the communication baudrate for the SCI Bootloader!")
parser.add_argument("-p", required=True, help="set the serial device address (/dev/ttySx)")
parser.add_argument("-k", required=True, help="path to the flash kernel file")
parser.add_argument("-a", required=True, help="path to the application file")
parser.add_argument("-d", required=True, help="The name of the device to load to", choices=["f2802x", "f2803x", "f2805x", "f2806x", "f2837xD", "f2837xS", "f2807x"])
parser.add_argument("-b2", help="second baudrate for flashing the program. The Flash API Can handl ehigher baudrates than the SCI Bootloader! -- Defaults to -b which defaults to 9600 --")
parser.add_argument("-debug", action="store_true", help="enable debug logging")

args = parser.parse_args()

MAX_AUTOBAUD = 10

if args.debug:
    logging.basicConfig(level=logging.DEBUG)
else:
    logging.basicConfig(level=logging.INFO)
logging.debug("args: {}".format(args))

if not os.path.isfile(args.a):
    logging.error("The given application file path does not point to a file!")
    exit(1)
elif not os.path.isfile(args.k):
    logging.error("The given kernel file path does not point to a file!")
    exit(1)

with serial.Serial(port=args.p) as ser:
    ser.baudrate = int(args.b)
    ser.port = args.p
    ser.timeout = 1  # read timeout 5 seconds...
#    ser.write_timeout = 0.1  # write timeout 5 seconds...
    if ser.is_open:
        logging.debug("Serial Port opened succesfull")
    else:
        logging.error("Could not open serial device Port: {}".format(args.p))
        exit(1)

    gu32_SectorMask = 0xFF
    # Do Autobaud
    logging.debug("Starting Autobaud!")
    ser.write("A".encode())
    okay = False
    count = 0
    while not okay and count < MAX_AUTOBAUD:
        recData = ser.read()      
        if recData == "A".encode():
            okay = True
            count = 0
        else:
            wr = ser.write("A".encode())
            count +=1
    if count is MAX_AUTOBAUD:
        logging.error("Max Autobaud Tries exceeded!")
        exit(1)
    logging.debug("Kernel Autobaud Successfull")
    logging.info("Downloading Kernel file to Controller...")
    with open(args.k, "rt") as kf:
        data = kf.read().replace("\n","").split(" ")
        bar = progressbar.ProgressBar(maxval=len(data), widgets=[progressbar.Bar("=", "[", "]"), " ", progressbar.Percentage()])
        bar.start()
        for i, b in enumerate(data):
            ser.write(bytes([int(b, 16)]))
            recData = ser.read(1)
            if not recData == bytes([int(b, 16)]):
                logging.error("recieved byte did not match sent!\n{} != {}\tPOS:{}\naborting...".format(recData, bytes([int(b, 16)]), i))
                exit(1)
            bar.update(i+1)
    bar.finish()
    sys.stdout.write("\n")
    sys.stdout.flush()

    logging.info("Flash kernel succesfully transferred to device.")

    for i in range(1,5)[::-1]: # Wait a few Seconds for the Flash kerne to boot. (the "5" is taken from the ti sample code)
        sys.stdout.write("\r")
        sys.stdout.write("Waiting for flash kernel to boot: {:2}".format(i))
        sys.stdout.flush()
        time.sleep(1)
    sys.stdout.write("\n")
    sys.stdout.flush()
    # Do Autobaud
    if args.b2:
        try:
            baud2 = int(args.b2)
        except:
            logging.error("value passed for b2 must be an integer!")
            exit(1)
        ser.baudrate = baud2 
    logging.debug("Starting Autobaud!")
    ser.write("A".encode())
    okay = False
    i = 0
    count = 0
    while not okay and count < MAX_AUTOBAUD:
        recData = ser.read()
        if str(recData.decode()) == "A":
            okay = True
            count = 0
        else:
            ser.write("A".encode())
            count += 1
    if count is MAX_AUTOBAUD:
        logging.error("Max Autobaud Tries exceeded!")
        exit(1)
    logging.debug("Application Autobaud Successfull")

    checksum = 0
    txCount = 0
    with open(args.a, "rt") as af:
        data = [a for a in af.read().split(" ")]
        logging.debug("Start sending first 22 bytes from file to DSP")
        bar = progressbar.ProgressBar(maxval=len(data), widgets=[progressbar.Bar("=", "[", "]"),  " ", progressbar.Percentage()])
        bar.start()
        i = 0
        for by in data[:22]: # Info on that can be found in the flash_kernel source itself. I did not find any on that in the documentation, at least not what they are transferring here.
            checksum = checksum + int(by, 16)
            ser.write(bytes([int(by, 16)]))
            bar.update(i+1)
            i += 1
        # waiting for flash kernel to erase the Flash. If done it will return the checksum of the sent data. (16 bit Integer)
        okay = False
        while not okay:
            retCheck = ser.read(2)
            if not retCheck:
                continue
            elif int(retCheck[::-1].hex(), 16) == checksum & 0xFFFF:
                okay = True
                checksum = 0
            else:
                logging.error("Returned Checksum did not match! //0// {:X} != {}".format(checksum, retCheck[::-1].hex()))
                exit(1)
         
        txCount = 0
        totalCount = 0
        wordData = 0x0000
        byteData = 0x0000
        # Send what comes after those reserved bytes
        for by in data[22:]:
            ser.write(bytes([int(by, 16)]))
            checksum = checksum + int(by, 16)
            bar.update(i+1)
            i += 1
            if txCount == 0: # read the length of the Data LSB
                wordData = int(by, 16)
            elif txCount == 1: # read the length of the Data MSB
                byteData = int(by, 16)
                wordData |= (byteData << 8)
            txCount += 1
            totalCount += 1
            if wordData == 0 and txCount > 1: # seems like there should be no 0 within the data? 
                wordData = 0
                byteData = 0
                break
            elif txCount == (2 * (wordData + 3)): # twice the wordData because of sending just 1 byte and not 16 bits - no idea where the "+3" comes from (taken from sample code, can be confirmed in the flash_kernel source) 
                okay = False
                while not okay:
                    retCheck = ser.read(2)
                    if not retCheck:
                        continue
                    elif int(retCheck[::-1].hex(), 16) == checksum & 0xFFFF:
                        okay = True
                        checksum = 0
                    else:
                        logging.error("Returned Checksum did not match! //1// {:X} != {}".format(checksum, retCheck[::-1].hex()))
                        exit(1)
                    wordData = 0
                    byteData = 0
                    txCount = 0
            elif (txCount - 6) % 0x800 == 0 and txCount > 6: # if the already sent data exceeds the device buffer (check flash_kernel source for mor info on how its done) checksum is returned and the program is flashed. Continue after that. 
                okay = False
                while not okay:
                    ser.timeout = 5
                    retCheck = ser.read(2)
                    ser.timeout = 1
                    if not retCheck:
                        continue
                    elif int(retCheck[::-1].hex(), 16) == checksum & 0x00FFFF:
                        okay = True
                        checksum = 0
                    else:
                        logging.error("Returned Checksum did not match! //2// {:X} != {}".format(int(hex(checksum), 16), retCheck[::-1].hex()))
                        exit(1)
        bar.finish()
        logging.info("Application loaded Successful!")
        logging.debug("--- %{} seconds ---".format(time.time() - start_time)) 
        exit(0)

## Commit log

2017-07-20 adding the initial version of the Python TAPAS-demo- app, TAPASstart.py contains the application itself, TAPASComm.py contains the SPI-Communication implementation and CRC
2017-07-25 added a first patch for an existing motorware installation to bring in all necessary changes for using the TAPAS-platform with motorware this patch can only be used for an installation of motorware_1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
2017-07-25 added the installation sources for TI's motorware_1_01_00_16, this has to be installed and patched to be used with TAPAS
2017-07-25 added the GUICOMPOSER-Webapp for TAPAS, just unpack, copy the webapps-folder and start with the board, can do identification and IO-control
2017-07-25 adding the design-files for the TAPAS-housing, the archive contains two files for the TOP and the BOTTOM part, ready to be 3D-printed
2017-07-26 update for GND-Pins done
2017-07-26 added current schematic for the TAPAS-Board, components that are not populated at the board per default, are crossed out in the document
2017-07-26 added file-extensions to symbolic links to ease the usage for windows users, further some files had to be renamed to avoid double names
    [TAPASCommV1_0.py, TAPASstartV1_0.py]
2017-07-26 inserted a section for the differences of the TAPAS development-version to version 1.0
2017-07-26 continued inserting
2017-07-26 added hints to TVS-diode, polymer-capacitor and isolation ICs
2017-08-17 added notice for enhanced current sensor on TAPAS
2017-09-07 I changed the SPI-CS pin that is used by the Raspberry Pi to communicate with the TAPAS-Board From now on, the DIP-switch position has to be ON-OFF-OFF-OFF seen from position 1 to position 4
2017-10-09 adding a first version of a Fritzing part for the TAPAS-Board. the logic-level terminals are connectable, but not the JTAG, io-PORT and the power terminals
2017-10-09 added some files including an image of the IOT2000<->TAPAS connection setup and the fritzing sources used to create the fritzing wiring image. a pdf including some pin numbers shall complete this fir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
    [SPI_Verkabelung IOT2040--TAPAS.fzz]
2017-10-10 bug fix in the platform differentiation
    [TAPASCommV1_0.py, TAPASstartV1_0.py]
2017-10-10 Added a section for using TAPAS with the IOT2000
    added images and some Fritzing parts and a project file together with a short description section about what to do
    for using the IOT2000 to communicate to the TAPAS board via SPI
2017-11-29 update Timestamp of the source
    the date on the Raspberry Pi was not correctly set before pushing the changes
2017-11-29 here comes the new patch for motorware_1_01_00_16, it will create two folders at board level directory; one folder that contains everything needed for TAPAS, another folder that contains everything n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
2017-11-29 now updated the symlink to the new patch for motorware.
2017-11-30 updated the DIP switches
    as the DIP switches are differently connected on TAPAS as they are on FIKAT,
    i updated the positions and the quick-start python script so that they now work with both
    boards, TAPAS as well as FIKAT
2017-12-11 renamed the webapp-Archive; the version that is contained here is intended for use with the pre-production board FIKAT that has the 20A-current sensors onboard
2017-12-11 added new webapps to be used with the current TAPAS-Board containing 30A current sensors further added code to catch the error of a negative acceleration value
    two archives are delivered, one is configured to be used with the
    OLIMEX TMS320-XDS100-V2 JTAG Debugger, the other one is setup to be used with
    the OLIMEX TMS320-XDS100-V3 JTAG Debugger
2017-12-11 renamed the webapp for the pre-prduction FIKAT-Board once again, now the folder inside the zip-archive has the correct name, further the configured JTAG-Debugger is getting visible
2017-12-11 created another archive for the pre-production FIKAT-Board to be used with the OLIMEX TMS320-XDS100-V3 JTAG-debugger
2018-03-06 added a small detail in the schematic
2018-03-06 renewed the symlink to the TAPAS-Schematic
2018-03-06 Here comes the assembly diagram for the TAPAS-Board.
2018-07-16 Adding the BOM for TAPAS-Board Version 1.0
    [TAPAS-V1.0_BOM.xlsx]
2018-09-17 updated the TAPAS-Schematic
